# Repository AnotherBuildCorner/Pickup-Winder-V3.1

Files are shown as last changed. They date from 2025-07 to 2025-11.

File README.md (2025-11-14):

# IN PROGRESS
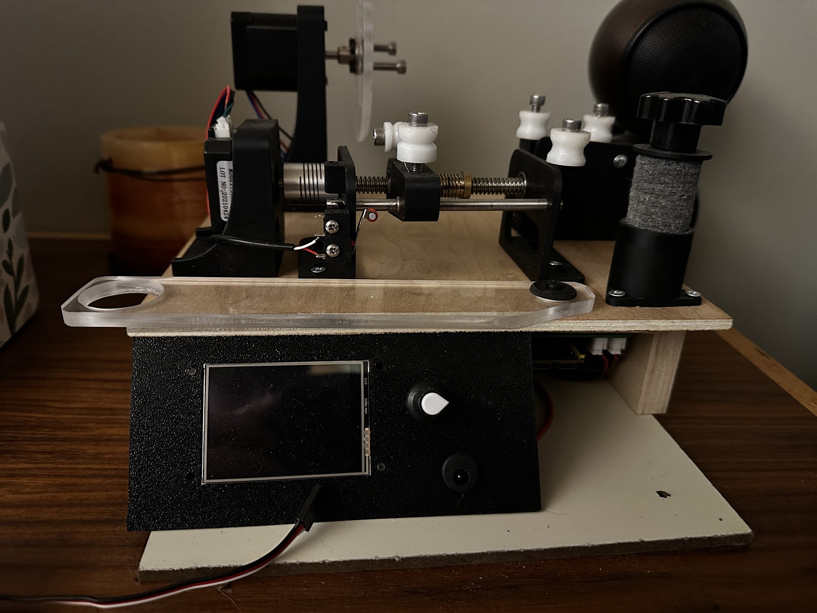
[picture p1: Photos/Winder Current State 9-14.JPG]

## Warning
Let's just get this out of the way. This is NOT a project for the faint of heart. A combination of mechanical aptitude, pinning electrical connectors, and a 3D printer are required to execute.
If you want a less advanced yet still capable version. Try the V2 winder based on commonly avaliable RC components.

With that out of the way. Let's begin.

## Background

On some level, this build is not so much an evolution, but a return to the original plan.
See, the very first computerized winder I had attempted used a pancake stepper and 12V power. But due to problems integrating the servo control and stepper libraries, this was quickly abandoned in favor of hobby RC components.
Now, with years more experience, and a better understanding of my inital failures, i'm back to make my ultimate CNC winder!

Heres the intended improvements.

* Increased Precision:

    The previous winder design utilized RC servos for traverse control. While this worked well, there are three major failing points.
    * 1: The servo has some measure of backlash, negating some precision.
    * 2: Using just the servo horn for traverse means complex Rotation-Linear position math.
    * 3: The largest failure. The servo traverse can only be controlled in 1 degree increments. With a 10mm arm length, this is 0.2mm per step.  Not precise enough for laying 42 gauge wire side by side.

    The new design uses a 2mm pitch lead screw, with 16 part microstepping. Or 3200 steps per revolution Which results in Linear precision of 0.000625mm.
    10X the required precision for layer to layer position of 44AWG wire (0.058mm with insulation). 

* Tension Measurement:
    A weakness of all previous designs was a reliance on "eye-caliper" measurements for tension. Otherwise known as trial and error.
    And knowing when the wire was close to it's breaking point was all but impossible. 
    To fix this problem, A HX711 chip paired to a 0-100g load cell was added for tension measurement. At minimum this provides a warning for break tension.

* Complete Offline Running:
    While previous versions were relatively easy to use. They were required to be connected to a computer for parameter adjustment.
    Perfectly acceptable for a hobbyist builder, With Arduino IDE being easy to access. But this is still less than ideal, and certainly not up to being an "ulitmate" winder.

* Preset and parameter Storage:
    This is part of the previous problem. While presets could be loaded into IDE and then selected via a selectable parameter in code. This still required modification to the code files any time a new pickup was desired.
    This new winder incorporates a small touch screen to allow parameter editing, and multiple presets than can be tweaked before deployment. (say a 5% underwind while maintaining all other specifications).

## Mechanicals
The core mechanical parts are composed of:
* Nema 17 Stepper full size motor. (Spindle Direct Drive)
    * Connected to 5mm flange adapter 
* Nema 17 Pancake Stepper motor (Traverse, could use full size here)
    * Connected to 8mm x 2 leadscrew with flexible coupler
    * Screw rides in two 8mm ID flange bearings
    * Traverse guide with anti-backlash nut, and 5mm guide rod with 5mm bushing

* Tensionser is a pair of felt Hi-Hat washers with bolt through center
* Tension meter is HX711 connected to a 0-100g load cell.
* Guides are cut from HDPE sheet. Future iterations may upgrade to PTFE guides as required.

Design notes:
While the position of most of the guides is somewhat critical. The one that matters the most is the final guide before the bobbin. Previous iterations placed this guide on top of the linear guide rail, not the lead screw. However, even with the guide bushings, the traverse carrier has some play over the guide. so during direction switches the accuracy would go down.
With the guide positioned over the screw, the maximum precision is reached as all backlash is taken up by the nut, and the guide over the rail is simply a direction change post.

Previous considerations used a 3 point tension meter setup, but in practice this is unnessecary. And ultimately made threading the guides more difficult. Use a small weight of known mass and calibrate the scale factor.

With the current design, alignment of the different components is challenging. In the future, incorporating the stepper and carrier brackets would be preferable, as well as a thin baseplate to align all the separate brackets.

Tension accuracy might be questionable.  With each individual guide a small amount of friction is added, but the exact quantity is unknown.

## Electricals
* Custom made Connection PCB populated with 
* 2x TMC2209 Stepper motor drivers
* Linear Voltage regulator breakout
* Esp32 S3 devkit Microprocessor
* HX711 Load cell amplifier
* SPI connected 2.4" touchscreen
* Connections made via JST connectors.
* 24VDC Power Supply
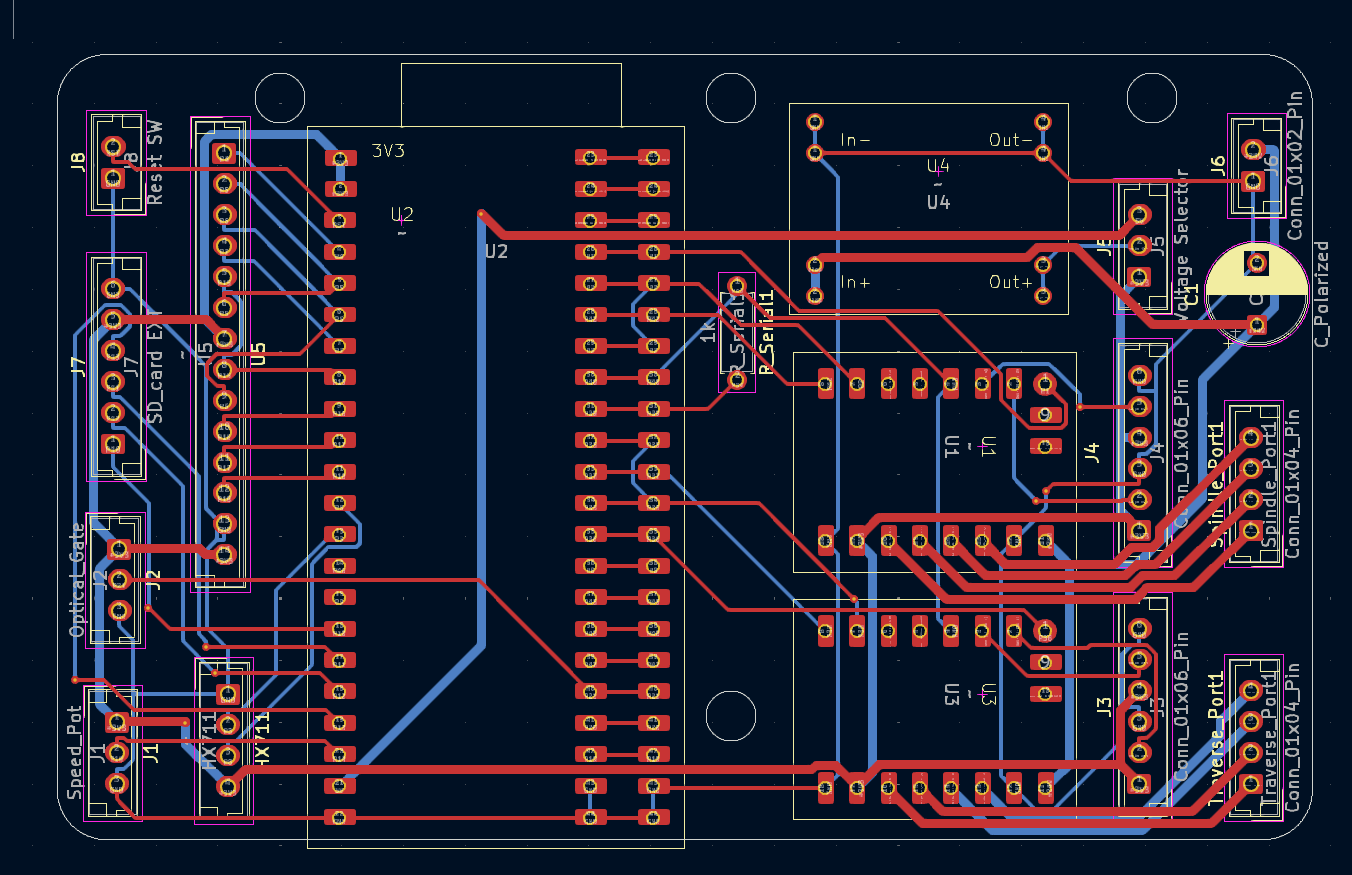
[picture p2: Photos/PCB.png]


Design Notes:
As previously touched upon. Previous iterations ran off of either an Arduino Nano or ESP32-Wroom. And lacked any meaningful interface aside from a speed control knob.
This new system adds the most powerful ESP32 available, and controls the steppers via modifiable hardware timers, allowing for pinpoint precision. 
The new stepper drivers are linked by the single channel UART communication. This allows for programming the microsteps and current limits in the code, no need for jumpers. However, there are also two open 6 port connectors designed to control microstep jumpers if needed.

Currently there is a provision to add a SD card, external reset switch, and an optical gate. The SD card port could also be used for some sort of sensor. The optical gate is currently connected to a limit switch instead of an optical gate. The original plan was to use a function in the 2209 to set zero, but this failed.

One step "backward" is the system no longer has a closed loop feedback on the spindle. However in practice no steps are dropped. and from experience if enough torque to drop a step is encountered, the stepper will drive backwards and ruin the bobbin anyways. So closed loop control is an unnessecary extra. 

There is currently an Error in the spacing of the microcontroller pins. The wider spaced outline fits correctly, however the narrow spacing, designed for a narrower S3 board, is too narrow.

## Interface
(In progress)

## Notes

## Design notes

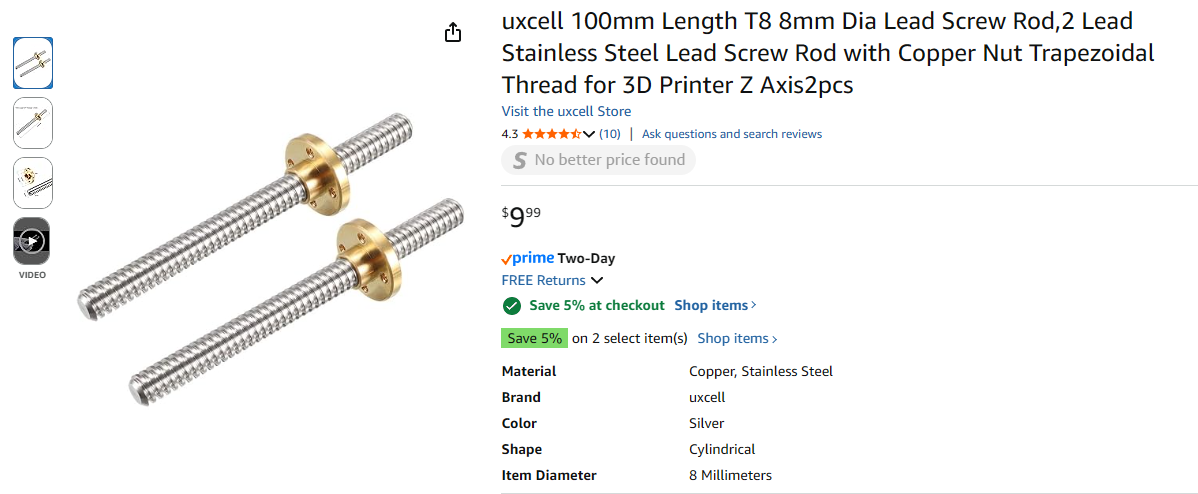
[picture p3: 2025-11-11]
Photos/Lead Screw.png

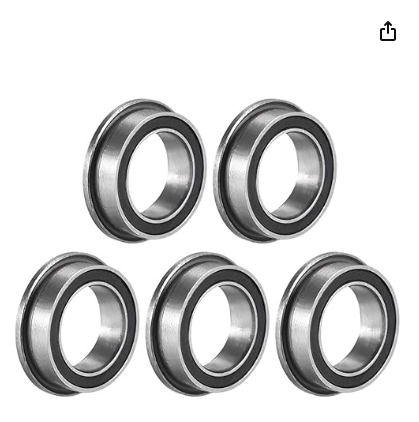
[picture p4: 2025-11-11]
Photos/Bearing 2.png

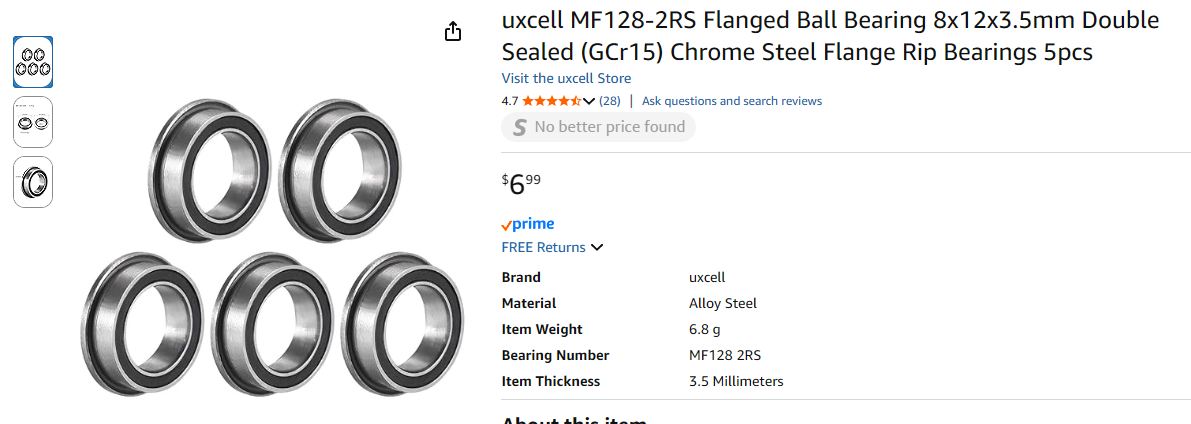
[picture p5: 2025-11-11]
Photos/Bearing.png

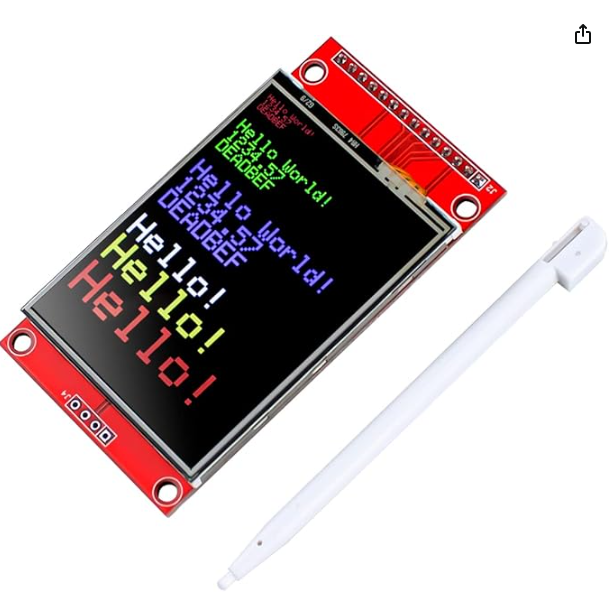
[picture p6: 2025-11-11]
Photos/Touchscreen2.png

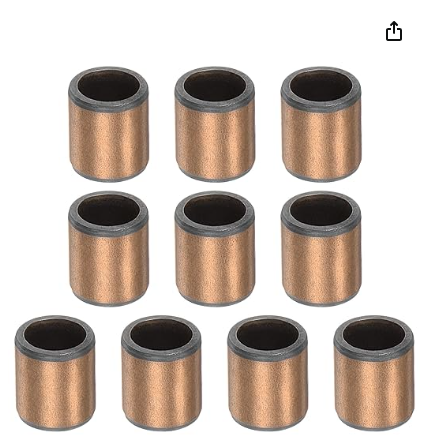
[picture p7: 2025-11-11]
Photos/Bushing 2.png

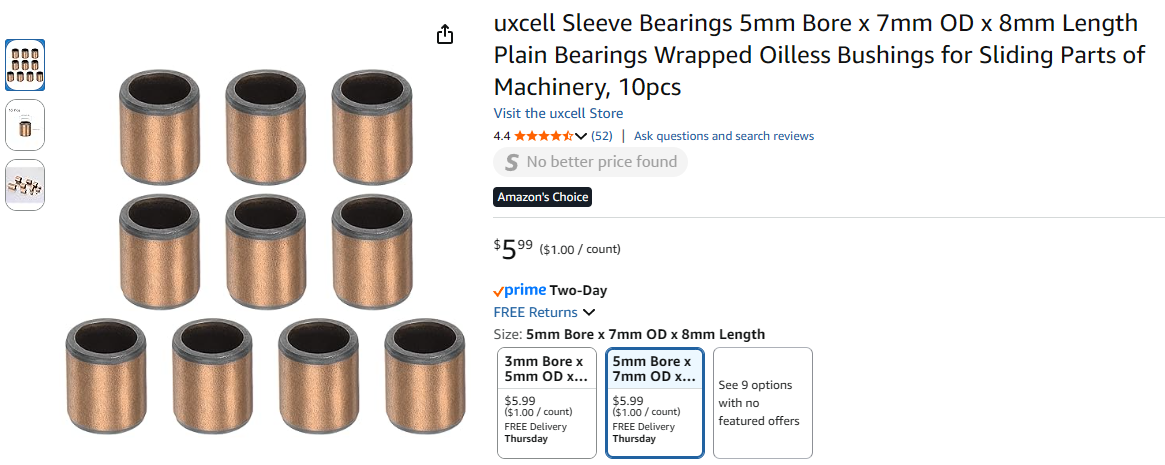
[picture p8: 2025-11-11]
Photos/Bushing.png

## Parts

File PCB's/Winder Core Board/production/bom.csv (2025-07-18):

Designator | Footprint | Quantity | Value | LCSC Part #
C1 | CP_Radial_D8.0mm_P5.00mm | 1 | C_Polarized
HX711 | JST_EH_B4B-EH-A_1x04_P2.50mm_Vertical | 1 | ~
J1 | JST_EH_B3B-EH-A_1x03_P2.50mm_Vertical | 1 | Speed_Pot
J2 | JST_EH_B3B-EH-A_1x03_P2.50mm_Vertical | 1 | Optical_Gate
J3, J4 | JST_EH_B6B-EH-A_1x06_P2.50mm_Vertical | 2 | Conn_01x06_Pin
J5 | JST_EH_B3B-EH-A_1x03_P2.50mm_Vertical | 1 | Voltage Selector
J6 | JST_EH_B2B-EH-A_1x02_P2.50mm_Vertical | 1 | Conn_01x02_Pin
J7 | JST_EH_B6B-EH-A_1x06_P2.50mm_Vertical | 1 | SD_card EXT
J8 | JST_EH_B2B-EH-A_1x02_P2.50mm_Vertical | 1 | Reset SW
R_SERIAL1 | R_Axial_DIN0207_L6.3mm_D2.5mm_P7.62mm_Horizontal | 1 | 1k
SPINDLE_PORT1, TRAVERSE_PORT1 | JST_EH_B4B-EH-A_1x04_P2.50mm_Vertical | 2 | Conn_01x04_Pin
U1, U3 | TC2209 | 2 | ~
U2 | S3 DEvkit DualW | 1 | ~
U4 | MS1584_fullboard | 1 | ~
U5 | JST_EH_B14B-EH-A_1x14_P2.50mm_Vertical | 1 | ~

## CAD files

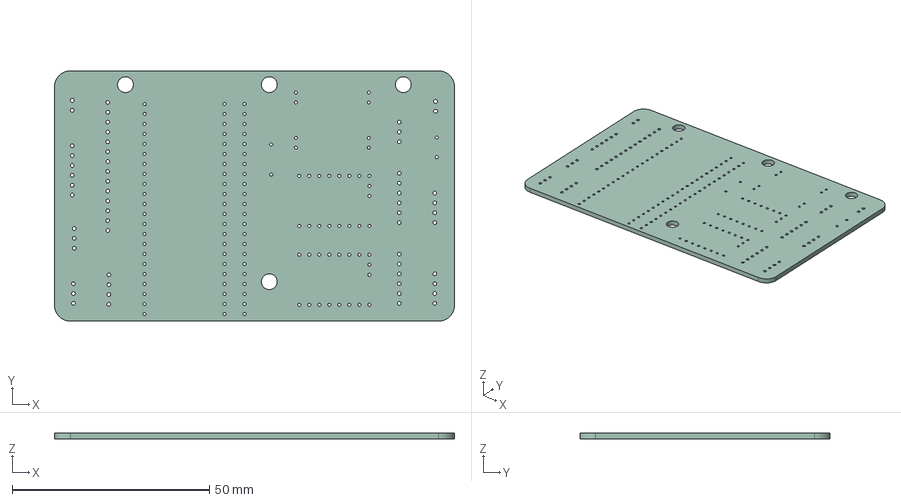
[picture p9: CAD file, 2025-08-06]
PCB's/Winder Core Board/Winder Core Board.step
101.5 x 63.5 x 1.51 mm

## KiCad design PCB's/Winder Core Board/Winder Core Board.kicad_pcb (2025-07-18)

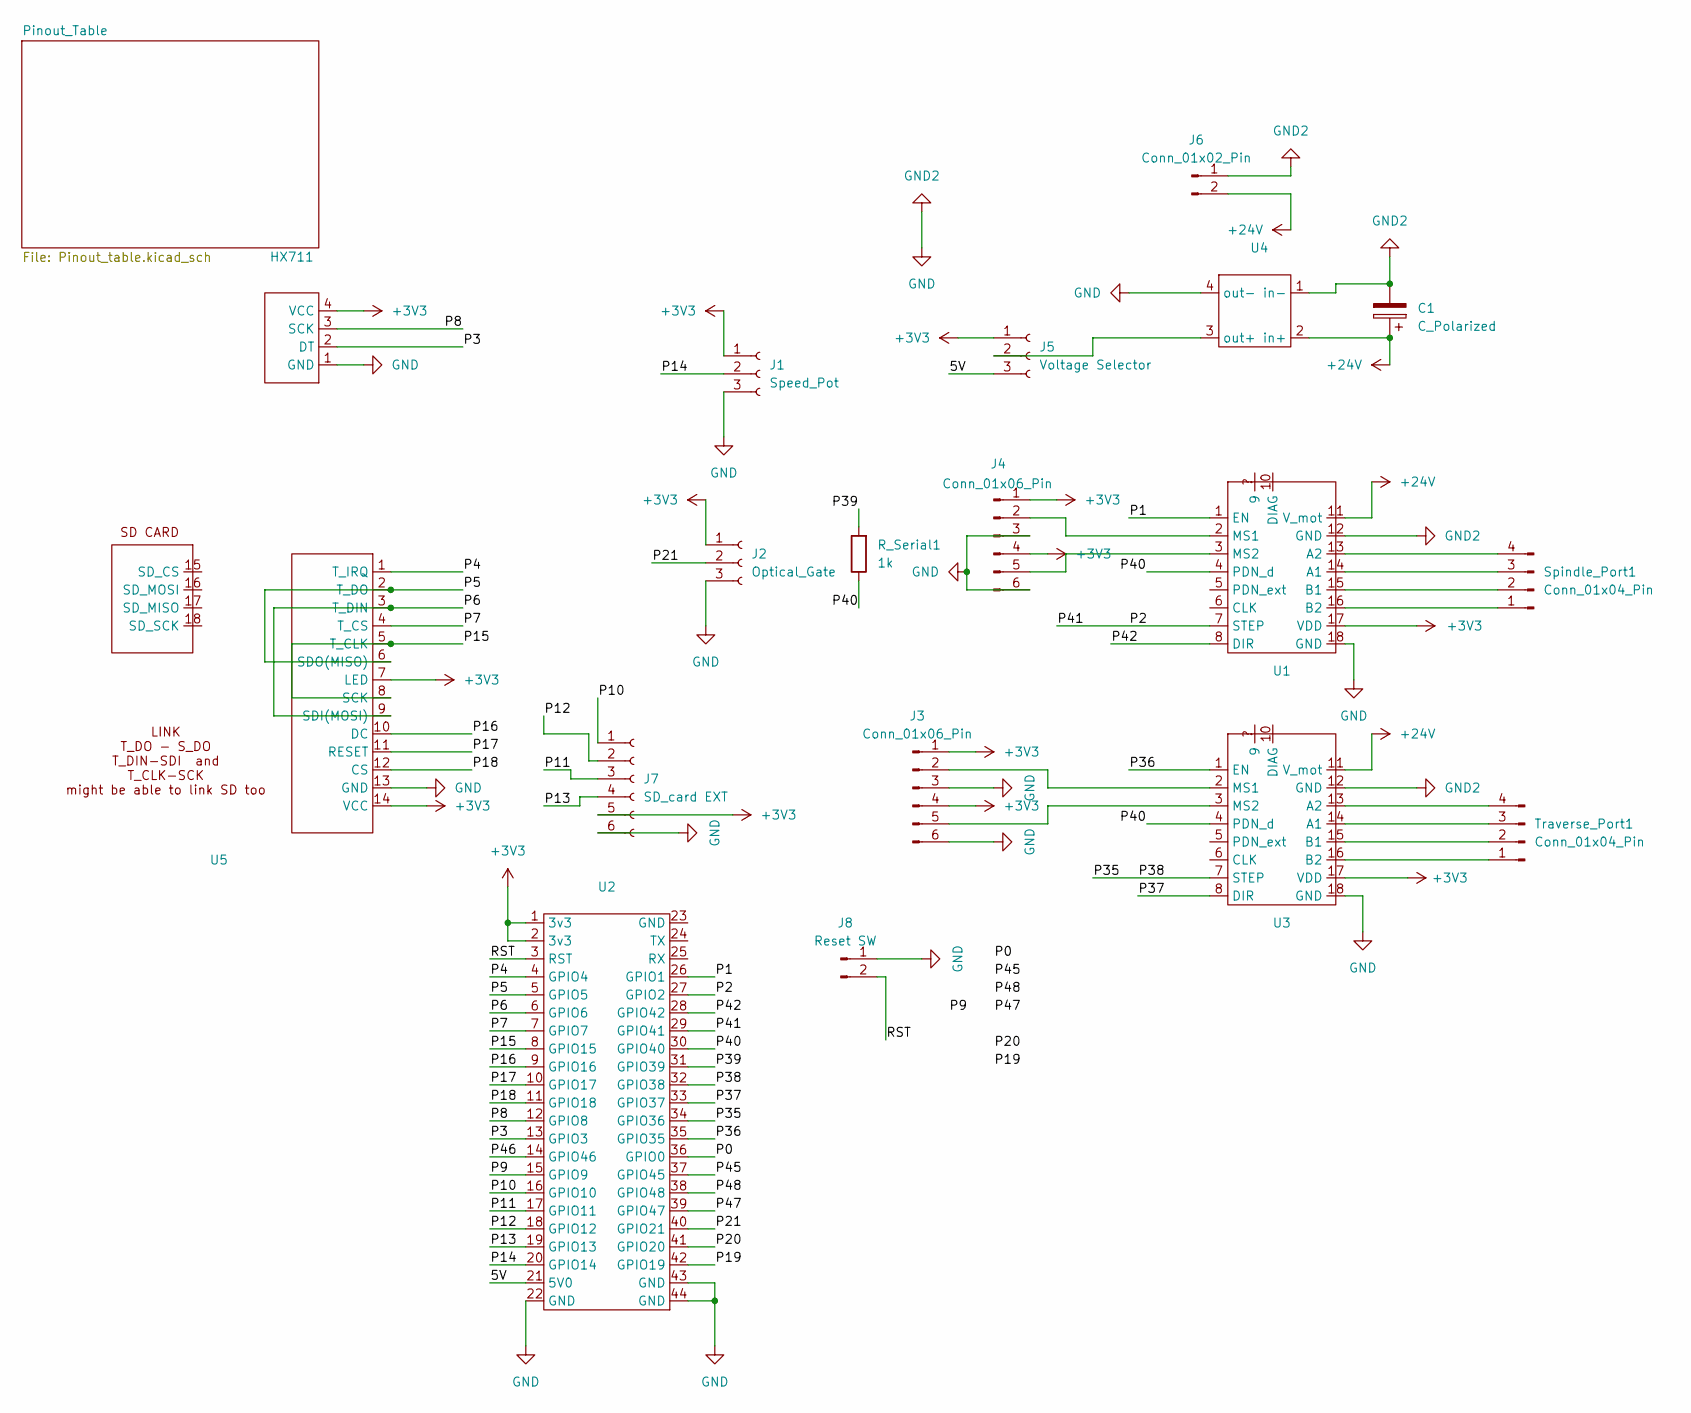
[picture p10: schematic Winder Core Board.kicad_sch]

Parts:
C1: C_Polarized; CP_Radial_D8.0mm_P5.00mm
HX711: JST_EH_B4B-EH-A_1x04_P2.50mm_Vertical
J1: Speed_Pot; JST_EH_B3B-EH-A_1x03_P2.50mm_Vertical
J2: Optical_Gate; JST_EH_B3B-EH-A_1x03_P2.50mm_Vertical
J3, J4: Conn_01x06_Pin; JST_EH_B6B-EH-A_1x06_P2.50mm_Vertical
J5: Voltage Selector; JST_EH_B3B-EH-A_1x03_P2.50mm_Vertical
J6: Conn_01x02_Pin; JST_EH_B2B-EH-A_1x02_P2.50mm_Vertical
J7: SD_card EXT; JST_EH_B6B-EH-A_1x06_P2.50mm_Vertical
J8: Reset SW; JST_EH_B2B-EH-A_1x02_P2.50mm_Vertical
R_Serial1: 1k; R_Axial_DIN0207_L6.3mm_D2.5mm_P7.62mm_Horizontal
Spindle_Port1: Conn_01x04_Pin; JST_EH_B4B-EH-A_1x04_P2.50mm_Vertical
Traverse_Port1: Conn_01x04_Pin; JST_EH_B4B-EH-A_1x04_P2.50mm_Vertical
U1, U3: TC2209
U2: S3 DEvkit DualW
U4: MS1584_fullboard
U5: JST_EH_B14B-EH-A_1x14_P2.50mm_Vertical

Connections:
+3V3: HX711.4 (VCC), J1.1, J2.1, J3.1, J3.4, J4.1, J4.4, J5.1, J7.5, U1.17 (VDD), U2.1 (3v3), U2.2 (3v3), U3.17 (VDD), U5.7 (LED), U5.14 (VCC)
+24V: C1.1, J6.2, U1.11 (V_mot), U3.11 (V_mot), U4.2 (in+)
/5V: J5.3, U2.21 (5V0)
/P0: U2.36 (GPIO0)
/P1: U1.1 (EN), U2.26 (GPIO1)
/P2: U1.7 (STEP), U2.27 (GPIO2), U2.29 (GPIO41)
/P3: HX711.2 (DT), U2.13 (GPIO3)
/P4: U2.4 (GPIO4), U5.1 (T_IRQ)
/P5: U2.5 (GPIO5), U5.2 (T_DO), U5.6 (SDO(MISO))
/P6: U2.6 (GPIO6), U5.3 (T_DIN), U5.9 (SDI(MOSI))
/P7: U2.7 (GPIO7), U5.4 (T_CS)
/P8: HX711.3 (SCK), U2.12 (GPIO8)
/P9: U2.15 (GPIO9)
/P10: J7.1, U2.16 (GPIO10)
/P11: J7.3, U2.17 (GPIO11)
/P12: J7.2, U2.18 (GPIO12)
/P13: J7.4, U2.19 (GPIO13)
/P14: J1.2, U2.20 (GPIO14)
/P15: U2.8 (GPIO15), U5.5 (T_CLK), U5.8 (SCK)
/P16: U2.9 (GPIO16), U5.10 (DC)
/P17: U2.10 (GPIO17), U5.11 (RESET)
/P18: U2.11 (GPIO18), U5.12 (CS)
/P19: U2.42 (GPIO19)
/P20: U2.41 (GPIO20)
/P21: J2.2, U2.40 (GPIO21)
/P35: U2.32 (GPIO38), U2.34 (GPIO36), U3.7 (STEP)
/P36: U2.35 (GPIO35), U3.1 (EN)
/P37: U2.33 (GPIO37), U3.8 (DIR)
/P39: R_Serial1.2, U2.31 (GPIO39)
/P40: R_Serial1.1, U1.4 (PDN_d), U2.30 (GPIO40), U3.4 (PDN_d)
/P42: U1.8 (DIR), U2.28 (GPIO42)
/P45: U2.37 (GPIO45)
/P46: U2.14 (GPIO46)
/P47: U2.39 (GPIO47)
/P48: U2.38 (GPIO48)
/RST: J8.2, U2.3 (RST)
GND: C1.2, HX711.1 (GND), J1.3, J2.3, J3.3, J3.6, J4.3, J4.6, J6.1, J7.6, J8.1, U1.12 (GND), U1.18 (GND), U2.22 (GND), U2.43 (GND), U2.44 (GND), U3.12 (GND), U3.18 (GND), U4.1 (in-), U4.4 (out-), U5.13 (GND)
unnamed: J3.2, U3.2 (MS1)
unnamed: J3.5, U3.3 (MS2)
unnamed: J4.2, U1.2 (MS1)
unnamed: J4.5, U1.3 (MS2)
unnamed: J5.2, U4.3 (out+)
unnamed: Spindle_Port1.1, U1.16 (B2)
unnamed: Spindle_Port1.2, U1.15 (B1)
unnamed: Spindle_Port1.3, U1.14 (A1)
unnamed: Spindle_Port1.4, U1.13 (A2)
unnamed: Traverse_Port1.1, U3.16 (B2)
unnamed: Traverse_Port1.2, U3.15 (B1)
unnamed: Traverse_Port1.3, U3.14 (A1)
unnamed: Traverse_Port1.4, U3.13 (A2)

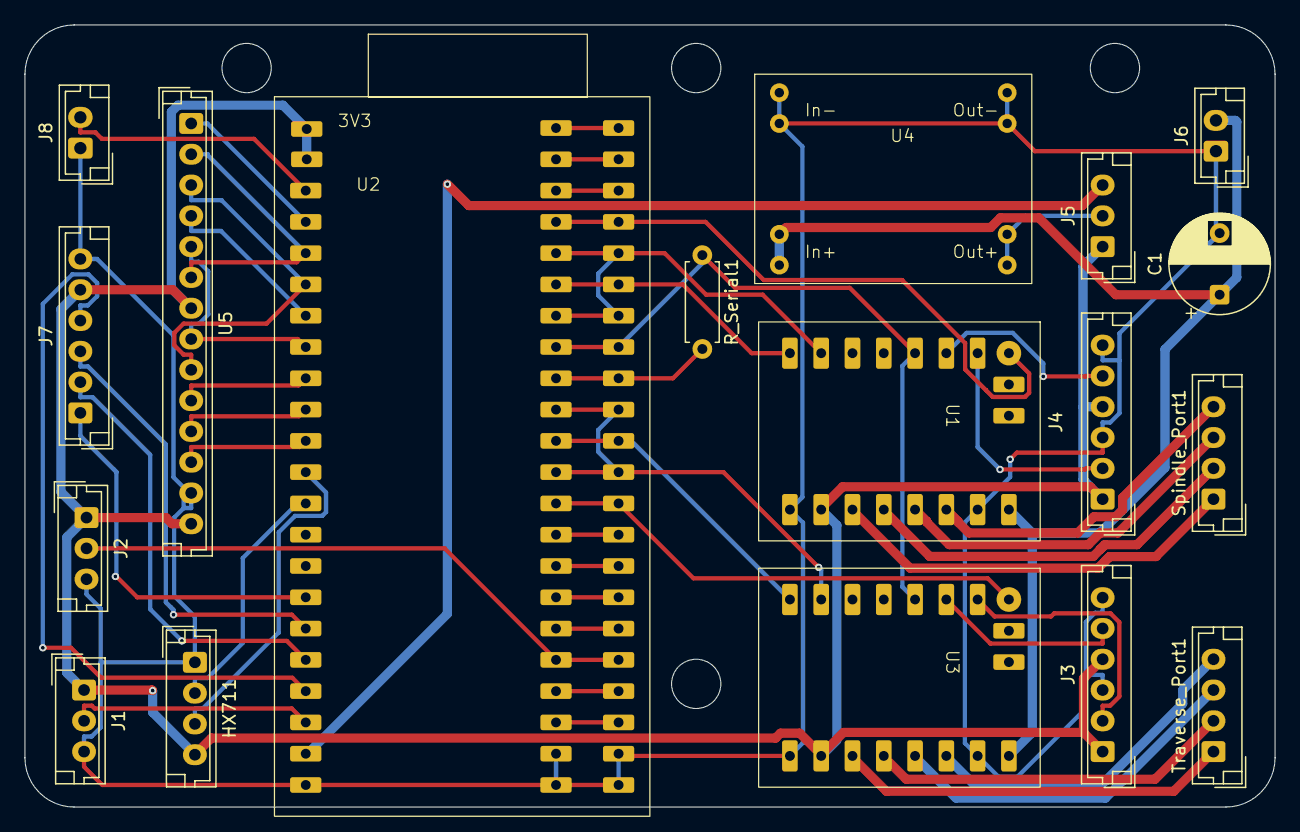
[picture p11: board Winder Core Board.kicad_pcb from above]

Board: 2 copper layers, 101.5 x 63.5 mm, 18 parts (0 on the bottom side), 42 nets.

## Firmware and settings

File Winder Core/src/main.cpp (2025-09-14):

#include <Arduino.h>
#include "ui.h"
#include <TFT_eSPI.h>
//#include "motion.h"
//#include "motion_HW.h"  // inside the ui.h
#include "wire_parameters.h"
#include "tensioner.h"
#include "main.h"

#define enable_screen true // Set to false to disable screen updates
int calibrationDone = 1;

void setup() {
  Serial.begin(115200);
  //SPIFFS.begin(true);

  delay(500);
  Serial.println("Did we boot?");
  

  
  loadDefaultPresets();   // Loads dummy preset data
  //initSD();
  initSPIFF();
  auto presets =  loadAllPresetsSPIFF();  //Work in progress
   presets =  loadAllPresets();  //Work in progress
  Serial.printf("Preset 1 name: %s\n",presets[1].name);
  
  if(enable_screen){
  initUI();     
  if(!calibrationDone) {
    runCalibration();      // Run calibration only if not done
  }}

 


    initMotionPins();
    delay(100);
    
    tensioner_setup();
    delay(100);
    initTMC();
    delay(100);
    traverse.enableHoming(DIAG_PIN, true); // Enable homing with active low
    traverse.compute_backoff(5.0f); // Set backoff distance to 10mm
  
}


void loop() {
  

  static unsigned long screentime = 0;
  static unsigned long speedtimer = 0;
  static unsigned long coretimer = 0; // initial speed in microseconds per step
  static unsigned long serialtimer = 0;
  unsigned long ct = micros();
  unsigned long ct2 = millis();
  static unsigned long traverse_timer = 0;
  static bool direction = 1;
  static bool homed = false;
  static bool runonce = false;
  bool printlines = false;

  if(serialtimer + 1000 < ct2 && printlines) {
    serialtimer = ct2;
    Serial.printf("Spindle Step Count: %d, Traverse Step Count: %d, Current Layer %d Traverse Direction: %s\n", spindleStepCount, traverseStepCount, currentLayer, traverseDir ? "Forward" : "Backward");
    Serial.printf("MAX dcr: %d, Computed Length: %d, Layer Count: %d Computed DCR: %d\n", MAX_dcr, calculated_length,  totalLayers,current_DCR );
  }
  


  if(!homed){homed = homeCycle(50, traverseDir, plateZeroOffset, ct2,100);}
    if(launchActive){
      if(!run){
        runonce = false;
        Current_RPM = 0;
      }

      timer_core_ms(ct2, 100); // Update core timer every 100ms
      windingScreenHandler(ct2, 100); // Update the winding screen every 100ms

      if(spindle.getTurnCount() >= currentPreset.turns*(1+currentPreset.overwind_percent)){
        run = false; }// Stop winding after 5000 turns}
      
      spindle.setEnabled(run);
      traverse.setEnabled(run);

        
      if(run && homed){ // Read the speed pot value and update target RPM
        if(!runonce){
          spindleStepCount = 0;
          traverseStepCount = 0;
          runonce = true;
          traverse.setDirection(traverseDir); // Set initial direction
        }
        ramp_handler(ct2, 100); // Handle spindle ramping every 100ms
        traverse_handler(ct2, 100); // Handle traverse movement every 100ms
        

  }}
  else{updateUI();
  tensioner_output(ct2, 100);}
}

//=-=-=-=-=-=-=-=-=-=-=-=-=-=-=-=-=-=-=-=-=-=-=-=-=-=-=-=-=-=-=-=-=-=-=-=-=-=-=-=-=-=-=-=-=-=-=-=-=-=-=-=-=-=-

void timer_core_ms(unsigned long timer_ms, int refresh_Time) {
  static unsigned long lastCoreTime = 0;
  if (timer_ms - lastCoreTime < refresh_Time) return; // Limit core updates to every 100ms
  lastCoreTime = timer_ms;
  turn_count = spindle.getTurnCount();
  tensioner_output(timer_ms, refresh_Time); // Update tensioner output

}


void ramp_handler(unsigned long timer_ms, int refresh_Time) {
        static unsigned long lastRampTime = 0;
        if(timer_ms - lastRampTime < refresh_Time) return; // Limit ramping to every 100ms

        if(spindle.getTurnCount() > currentPreset.turns*(1+currentPreset.overwind_percent)-spin_down_turns){spindle.rampAcceleration(10, Accel_RPM, true, timer_ms, refresh_Time);}
        else{spindle.rampAcceleration(Target_RPM, Accel_RPM, false, timer_ms, refresh_Time);}
        
         // Set traverse rate based on spindle speed and wire gauge
}


void traverse_handler(unsigned long timer_ms, int refresh_Time) {
  static unsigned long lastTraverseTime = 0;
  spindle.getRate(timer_ms, refresh_Time); // Read the speed pot value and update target RPM
  if (timer_ms - lastTraverseTime < refresh_Time) return; // Limit traverse updates to every 100ms
    lastTraverseTime = timer_ms;
    currentPosition=traverse.computePosition();
    traverse.setLimits(traverseStepCount);
    traverse.setMultiplier(); // Set multiplier based on current layer count
    current_multiplier = traverse.getMultiplier();
    traverse.setTraverseRate(Current_Step_Rate, .0635);
    traverse.controlPosition(); // Control position based on step count
    currentLayer = traverse.getLayerCount(); // Update current layer count


}

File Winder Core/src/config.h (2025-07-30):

#pragma once
// main parameters
#define Start_RPM 100
#define Accel_RPM 200 //rpm
#define maxrpm 1000
#define refreshRate 10
#define spin_down_turns 30
#define Lead_Screw_Pitch 2 //mm

// -------------- screen pins --------------
#define TOUCH_IRQ 4
#define TOUCH_CS  7


#define TFT_CS    18
#define TFT_DC    16
#define TFT_RST   17

#define TFT_MISO  5  //T_DO
#define TFT_SCLK  15  //T_CLK
#define TFT_MOSI  6  //T_DIN

#define SD_CS 10
#define SD_MOSI 11
#define SD_MISO 13
#define SD_SCK 12


#define SPEED_POT 14  //3
#define speedPotAveraging 10
#define speedPotChunk 20
//------------ Motion control pins ------------
#define SPINDLE_STEP_PIN    ((gpio_num_t)2)
#define SPINDLE_DIR_PIN     ((gpio_num_t)42)
#define SPINDLE_ENABLE_PIN  ((gpio_num_t)1)  // 41  1
#define SPINDLE_READBACK_PIN  ((gpio_num_t)41) // 40   45

#define SPINDLE_RX_PIN      ((gpio_num_t)40)
#define SPINDLE_TX_PIN      ((gpio_num_t)39)  //39 46
#define SPINDLE_MICROSTEPS 2

#define INIT_TRAVERSE true
#define TRAVERSE_STEP_PIN   ((gpio_num_t)38)
#define TRAVERSE_DIR_PIN    ((gpio_num_t)37)
#define TRAVERSE_ENABLE_PIN ((gpio_num_t)35)
#define TRAVERSE_READBACK_PIN ((gpio_num_t)36)

//#define TRAVERSE_RX_PIN      ((gpio_num_t)48)  // not in use
//#define TRAVERSE_TX_PIN      ((gpio_num_t)47)

#define TRAVERSE_MICROSTEPS 16
#define MAX_TRAVERSE_MULTIPLIER 10 // Maximum multiplier for traverse step rate

#define DIAG_PIN ((gpio_num_t)21)  //13
//-------------  tensioner pins ---------------
#define TENSIONER_READ_PIN 3   
#define TENSIONER_SCK_PIN 8
// ----------  ISR parameters -----------
#define ISR_delay 10 // microseconds   

// ---------- Math params --------------
#define micross 1000000
#define refreshmicros (micross / refreshRate)
#define steps_rev 200 //steps/rev
#define accel 200/steps_rev //rpm/second^2
#define RPM_to_micros 60* micross / (steps_rev * 2) // conversion factor from RPM to microseconds per step

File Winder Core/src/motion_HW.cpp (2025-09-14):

// motion.cpp
#include "motion_HW.h"
#include <driver/ledc.h>

#define R_SENSE 0.11f
#define Spindle_ADDRESS 0b00
#define Traverse_ADDRESS 0b01
#define ADC_MAX 4095
//#define DUAL_SERIAL
#define SENSORLESS_HOME

#ifdef DUAL_SERIAL
HardwareSerial& TMCSerial = Serial1;
HardwareSerial& TMCSerial_traverse = Serial2;
TMC2209Stepper spindle_driver(&TMCSerial, R_SENSE, Spindle_ADDRESS);
TMC2209Stepper traverse_driver(&TMCSerial_traverse, R_SENSE, Traverse_ADDRESS);
#else
HardwareSerial& TMCSerial = Serial1;
TMC2209Stepper spindle_driver(&TMCSerial, R_SENSE, Spindle_ADDRESS);
TMC2209Stepper traverse_driver(&TMCSerial, R_SENSE, Traverse_ADDRESS);
#endif

#define SPINDLE_TOFF
#define SPINDLE_BLANK_TIME 24
#define SPINDLE_SPREADCYCLE true
#define SPINDLE_PWM_AUTOSCALE true
#define SPINDLE_PWM_FREQ 2
#define SPINDLE_I_AUTOSCALE false
#define SPINDLE_RMS_CURRENT 2000 // RMS current in mA

#define TRAVERSE_TOFF 4
#define TRAVERSE_BLANK_TIME 24
#define TRAVERSE_SPREADCYCLE true
#define TRAVERSE_PWM_AUTOSCALE true
#define TRAVERSE_PWM_FREQ 2
#define TRAVERSE_I_AUTOSCALE false
#define TRAVERSE_RMS_CURRENT 600 // RMS current in mA

#define TRAVERSE_STALLGUARD 100// 0-255

void IRAM_ATTR onSpindleStep() {
  if(enableSpindleISR) {

  spindleStepCount++;
  
}}

void IRAM_ATTR onTraverseStep() {
  if(enableTraverseISR) {
    if(INIT_TRAVERSE) {    
      if(traverseDir) {
      traverseStepCount--;
    } else {
      traverseStepCount++;}}
    else{
    if(traverseDir) {
      traverseStepCount++;
    } else {
      traverseStepCount--;
    }}
  }

}

AxisStepper::AxisStepper(gpio_num_t stepPin, gpio_num_t dirPin, int ledcChannel, gpio_num_t enablePin, gpio_num_t readbackPin)
  : _stepPin(stepPin), _dirPin(dirPin), _enablePin(enablePin), _targetRate(0),
    _dirState(true), _stepCount(0), _ledcChannel(ledcChannel), _readbackPin(readbackPin) {}

void AxisStepper::begin(bool clockwise) {
  pinMode(_dirPin, OUTPUT);
  setDirection(clockwise);

  if (_enablePin != GPIO_NUM_NC) {
    pinMode(_enablePin, OUTPUT);
    gpio_set_level(_enablePin, HIGH);
  }

  // LEDC setup
  ledcSetup(_ledcChannel, 0, 1);  // 5 kHz default
  ledcAttachPin(_stepPin, _ledcChannel);
  

  // Count steps using interrupts
  pinMode(_readbackPin, INPUT);
  attachInterrupt(digitalPinToInterrupt(SPINDLE_READBACK_PIN), onSpindleStep, RISING);

  

}

void AxisStepper::setDirection(bool clockwise) {
  _dirState = clockwise;
  gpio_set_level(_dirPin, _dirState);
}

void AxisStepper::setEnabled(bool run) {
  if (_enablePin != GPIO_NUM_NC) {
    gpio_set_level(_enablePin, run ? LOW : HIGH);
    enableSpindleISR = run; // Enable or disable ISR based on run state
  }
}
void AxisStepper::getRate(unsigned long timer_ms, int refresh_Time) {
  static unsigned long lastReadTime = 0;
  static float averageRPM = 0;

  // Ring buffer for moving average
  static int rpmBuffer[5] = {0};
  static int bufferIndex = 0;
  static bool bufferFilled = false;

  if (timer_ms - lastReadTime < refresh_Time) return;
  lastReadTime = timer_ms;

  // Read and map pot value
  int potValue = analogRead(SPEED_POT);
  int RPM = map(potValue, 0, ADC_MAX, maxrpm, 0);

  // Store in buffer
  rpmBuffer[bufferIndex] = RPM;
  bufferIndex = (bufferIndex + 1) % speedPotAveraging;
  if (bufferIndex == 0) bufferFilled = true;

  // Compute average
  int sum = 0;
  int count = bufferFilled ? 5 : bufferIndex;
  for (int i = 0; i < count; i++) {
    sum += rpmBuffer[i];
  }
  averageRPM = sum /( count*speedPotChunk);
  averageRPM = (averageRPM *speedPotChunk);
  averageRPM = constrain(averageRPM, 0, maxrpm); // Ensure average is within bounds

  Target_RPM = averageRPM;
}


void AxisStepper::setRate(float RPM) {
  if (RPM > maxrpm) {
    RPM = maxrpm; } // Cap at max RPM
    else if (RPM < 0) {RPM = 0; } // Prevent negative RPM
  Current_RPM = RPM; // Update current RPM
  Current_Step_Rate = (RPM * steps_rev * SPINDLE_MICROSTEPS) / 60.0;
  ledcWriteTone(_ledcChannel, Current_Step_Rate);
}

void AxisStepper::rampAcceleration(int targetRPM, float ramp_rate, bool decelerate, unsigned long timer_ms ,int refresh_Time) {
  static unsigned long lastRampTime = 0;
  if(timer_ms - lastRampTime < refresh_Time) return; // Limit ramping to every 100ms
  lastRampTime = timer_ms;
    if (targetRPM > maxrpm) {targetRPM = maxrpm; } // Cap at max RPM
    else if (targetRPM < 0) {targetRPM = 0; } // Prevent negative RPM
  if(Current_RPM != targetRPM){ // Prevent negative RPM
    if(decelerate)
      {Current_RPM -= (ramp_rate*refresh_Time/1000);
      if(Current_RPM < targetRPM) {Current_RPM = targetRPM; } 
      }
    else
      {Current_RPM += (ramp_rate*refresh_Time/1000);
      if(Current_RPM > targetRPM) {Current_RPM = targetRPM; }}

    setRate(Current_RPM); // Update step rate
  }}


int AxisStepper::getStepCount() const {  // Read the global step count
  return spindleStepCount;
}

float AxisStepper::getTurnCount() const {
  return static_cast<float>(spindleStepCount) / ( steps_rev* SPINDLE_MICROSTEPS);
}

void AxisStepper::resetStepCount() {
  spindleStepCount = 0;
}

TraverseStepper::TraverseStepper(gpio_num_t stepPin, gpio_num_t dirPin, int ledcChannel, gpio_num_t enablePin, gpio_num_t readbackPin)
  : _stepPin(stepPin), _dirPin(dirPin), _enablePin(enablePin), _pos(0),
    _posMin(0), _posMax(1000), _homePin(GPIO_NUM_NC), _homeActiveLow(true), _homed(false), _ledcChannel(ledcChannel) {}

void TraverseStepper::setRPM(int RPM) {
  if (RPM > maxrpm) {
    RPM = maxrpm; } // Cap at max RPM
    else if (RPM < 0) {RPM = 0; } // Prevent negative RPM
    int Step_Rate = (RPM * steps_rev * TRAVERSE_MICROSTEPS) / 60.0;

  ledcWriteTone(_ledcChannel, Step_Rate);
}

void TraverseStepper::begin() {
  pinMode(_dirPin, OUTPUT);
  gpio_set_level(_dirPin, traverseDir);

  if (_enablePin != GPIO_NUM_NC) {
    pinMode(_enablePin, OUTPUT);
    gpio_set_level(_enablePin, HIGH);
  }

  ledcSetup(_ledcChannel, 0, 1);
  ledcAttachPin(_stepPin, _ledcChannel);

  pinMode(TRAVERSE_READBACK_PIN, INPUT);
  attachInterrupt(digitalPinToInterrupt(TRAVERSE_READBACK_PIN), onTraverseStep, RISING);

}

void TraverseStepper::setRate(float stepsPerSecond) {
  ledcWriteTone(_ledcChannel, stepsPerSecond);
}

void TraverseStepper::setEnabled(bool run) {
  if (_enablePin != GPIO_NUM_NC) {
    gpio_set_level(_enablePin, run ? LOW : HIGH);
    enableTraverseISR = run; // Enable or disable ISR based on run state
  }
}

void TraverseStepper::setLimits(int currentpos) {

  if(_holdPos == 0){
    _holdPos = currentpos;
  _posMin = _holdPos + distanceToSteps(_offset+_internal_error);
  _posMax = _holdPos + distanceToSteps(_offset+_width-_internal_error);
  Serial.printf("Min: %d Max: %d\n", _posMin, _posMax);
  }


}
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

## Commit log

2025-07-01 new push
    [Pinout_table.kicad_sch, Winder Core Board.kicad_pcb, Winder Core Board.kicad_sch]
2025-07-05 homing running
2025-07-06 DCR not working yet
    [global_vars.cpp, main.cpp, motion_HW.cpp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]
2025-07-07 working on FS. probably need to switch to SD
2025-07-18 PCB updated. moved some pins.
    [Pinout_table.kicad_sch, Winder Core Board.kicad_pcb, Winder Core Board.kicad_sch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]
2025-07-30 pins 35 and 36 flipped. board works.
    [config.h, global_vars.cpp, main.cpp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]
